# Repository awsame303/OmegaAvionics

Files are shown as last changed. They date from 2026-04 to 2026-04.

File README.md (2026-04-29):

# Omega Avionics — L1 Certification Rocket

Screenshot 2026-04-14 at 5 32 18 PM

A custom-built high-power rocket with a fully designed avionics bay, dual-deployment chute release system, and custom PCB — built to earn an **NAR/Tripoli L1 certification** (H & I class motors) :O

## Overview

This project combines mechanical engineering, embedded systems, and PCB design into a single flight vehicle. The goal is a rocket capable of flying on H and I class motors with onboard data logging, IMU-based orientation tracking, barometric altitude sensing, and an automated parachute deployment system. 

## Purpose

I made it because I wanted to expand my love for rocketry and actually learn a lot about data collection, how to make things that can survive high stress environments, and how to use fillets and other building related things. My ultimate goal for this project is to make a cool rocket that flighs high but also gives me valuable data that I can learn a lot about engineering and aerospace from. I was inspired from my TARC rocketry team, and ultimately wanted to build something with a bit more juice that can fly higher and be more stable. I think that if this goes well, it will be fun to build and assemble. I'm especially excited to paint it, because I heard that it's one of the most challening parts. 

## Hardware

### Avionics PCB



The custom PCB is the heart of the avionics bay, and I Designed it! from scratch in EasyEDA.

Screenshot 2026-04-26 at 9 55 04 AM
> I made another version without RF in case it doesn't work and I made it able to short the pins if I didn't want to use it. In case you were wondering why it wasn't on the PCBA or the BOM

Screenshot 2026-04-26 at 9 55 17 AM

## Firmware

Firmware is written for the ESP32-S3 

## CAD

Full rocket assembly modeled in Onshape
[Link](https://cad.onshape.com/documents/853f342d943e26935c21807b/w/3225035a6dba25a7b5e66f22/e/7ca1891e4b8cbf6983780e85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)

Simulation and stability analysis done in Openrocket



## Certification Goal

This rocket is being built to achieve JKUNIOR Level One High Power Cert through NAR or Tripoli. L1 certification allows ME to purchase and fly H and I class motors independently.

## License

MIT — do whatever u want w it

| Item / Part | Designator | Description / Purpose | Qty | Price | Source |
| :--- | :--- | :--- | :--- | :--- | :--- |
| AMS1117-3.3_C22466222 | U3 | Voltage regulator | 1 | $0.00 | LCSC |
| UBEC | RELE1 | Power module | 1 | $0.00 | LCSC |
| TPS62130RGTRF0 | U1 | Step-down converter | 1 | $0.00 | LCSC |
| ESP32-S3-WROOM-1(N8R2) | U4 | Main microcontroller | 1 | $0.00 | LCSC |
| 2.2uH | U2 | Power inductor | 1 | $0.00 | LCSC |
| 19-217/GHC-YR1S2/3T | LED1 | Status indicator | 1 | $0.00 | LCSC |
| TYPE-C 16PIN 2MD(073) | USB1 | USB interface | 1 | $0.00 | LCSC |
| BMP280 | U6 | Altimeter/Pressure sensor | 1 | $0.00 | LCSC |
| LED-0603_G | LED3 | Status indicator | 1 | $0.00 | LCSC |
| 2700Hz | BUZZER1 | Audible alert | 1 | $0.00 | LCSC |
| 1N4148W | D2 | Signal diode | 1 | $0.00 | LCSC |
| KH-6X6X4.3H-TJ | SW1 | Tactile switch | 1 | $0.00 | LCSC |
| D-MMBT2222A-7-F | U8 | NPN Transistor | 1 | $0.00 | LCSC |
| 470uF | C1 | Electrolytic capacitor | 1 | $0.00 | LCSC |
| 1N5819HW | D1 | Schottky diode | 1 | $0.00 | LCSC |
| Apogee 12in Parachute Protector | | For protecting the parachute from the ejection charge | 1 | $9.66 | Apogee Rocketry |
| emma kites 100% Kevlar Braided String 100Lb | | To attach the rocket to the parachute | 1 | $14.95 | Amazon |
| sprookber Stainless Steel Chain Quick Links | | To attach the parachute cord to the rocket | 1 | $8.99 | Amazon |
| Aero Pack 29/38mm Motor Adapter | | To mount mid power motors (G, F) before testing H class | 1 | $31.85 | Apogee Rocketry |
| 36" Printed Nylon Parachute | | To ensure smooth landing and protect electronics | 1 | $18.69 | Apogee Rocketry |
| Aero Pack 38mm Retainer | | Secures rocket motors during flight | 1 | $30.63 | Apogee Rocketry |
| Bob Smith BSI-205 Slow-Cure Epoxy (30-Min) | | Strong adhesive for structural components | 1 | $13.69 | Amazon |
| J-B Weld 8265S Original Cold-Weld | | Adhesive for miscellaneous parts | 1 | $6.54 | Amazon |
| LOC Forte Kit | | Primary airframe and basic rocket components | 1 | $95.97 | LOC Precision |

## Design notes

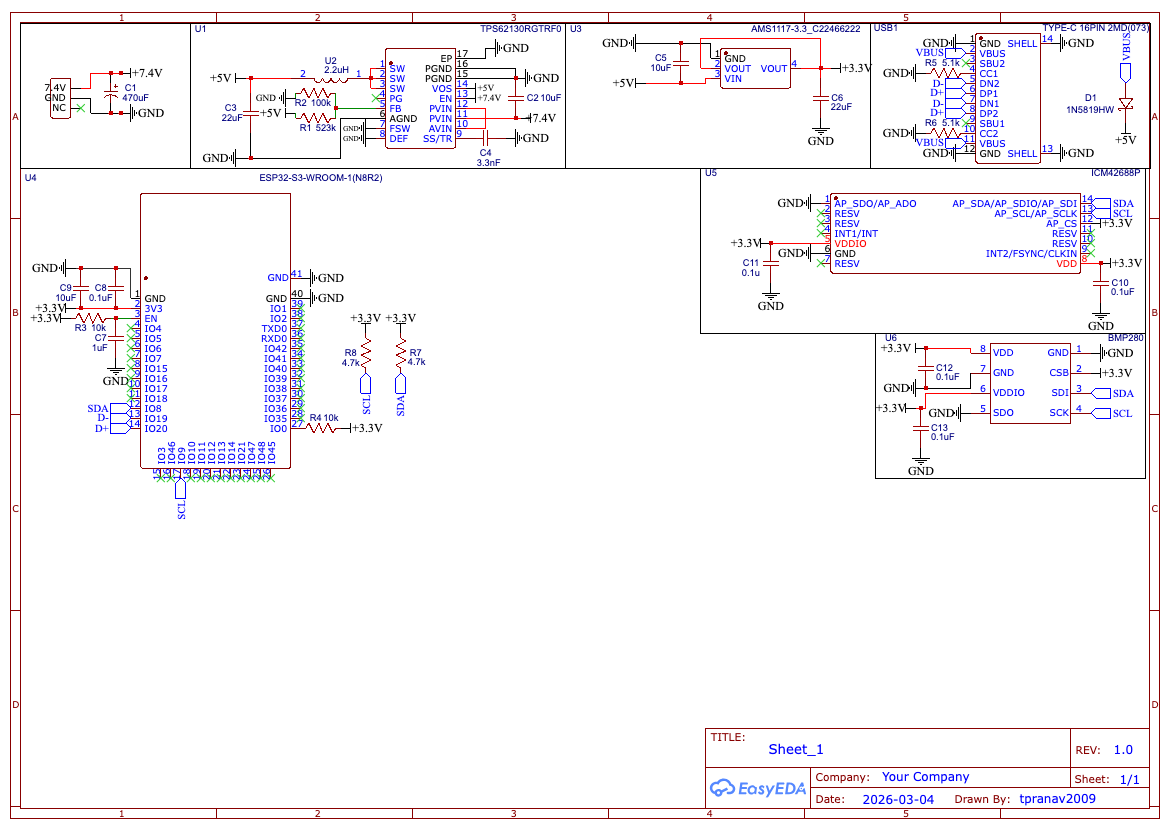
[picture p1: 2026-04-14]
Avionics/PCB/schematic.png

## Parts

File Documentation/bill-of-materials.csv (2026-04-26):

Name | Purpose | Quantity | Total Cost (USD) | Link | Distributor
AMS1117-3.3_C22466222 | U3 | 1 | 0.00 | https://item.szlcsc.com/410724.html | LCSC
UBEC | RELE1 | 1 | 0.00 |  | LCSC
TPS62130RGTRF0 | U1 | 1 | 0.00 | https://item.szlcsc.com/546058.html | LCSC
ESP32-S3-WROOM-1(N8R2) | U4 | 1 | 0.00 | https://www.mouser.cn/datasheet/2/891/Espressif_ESP32_S3_WROOM_1_1U_Preliminary-2530171.pdf | LCSC
2.2uH | U2 | 1 | 0.00 | https://atta.szlcsc.com/upload/public/pdf/source/20220713/554BEAF1208EE235D5D1578E7485E8C7.pdf | LCSC
19-217/GHC-YR1S2/3T | LED1 | 1 | 0.00 | https://item.szlcsc.com/347874.html | LCSC
TYPE-C 16PIN 2MD(073) | USB1 | 1 | 0.00 | https://atta.szlcsc.com/upload/public/pdf/source/20210409/C2765186_34D42616F62DF94D17C4D63D74D9FD03.pdf | LCSC
BMP280 | U6 | 1 | 0.00 | https://atta.szlcsc.com/upload/public/pdf/source/20200702/C83291_F39E84AB7DFC569A4C7554F8659640A1.pdf | LCSC
LED-0603_G | LED3 | 1 | 0.00 |  | LCSC
2700Hz | BUZZER1 | 1 | 0.00 | https://item.szlcsc.com/200842.html | LCSC
1N4148W | D2 | 1 | 0.00 | https://item.szlcsc.com/301422.html | LCSC
KH-6X6X4.3H-TJ | SW1 | 1 | 0.00 | https://item.szlcsc.com/14483.html | LCSC
D-MMBT2222A-7-F | U8 | 1 | 0.00 | https://www.diodes.com/assets/Package-Files/SOT23.pdf | LCSC
470uF | C1 | 1 | 0.00 | https://atta.szlcsc.com/upload/public/pdf/source/20250321/063FCEC07E4987B05CDB75E62EF93118.pdf | LCSC
1N5819HW | D1 | 1 | 0.00 | https://atta.szlcsc.com/upload/public/pdf/source/20210423/C2828417_EF1BF8BE3D48F97E320B09B073C89160.pdf | LCSC
Apogee 12in Parachute Protector | For protecting the parachute from the ejection charge of the parachute so it doesn't get burned | 1 | 9.66 | https://www.apogeerockets.com/Building-Supplies/Parachute-Protection/Cloth/Apogee-12in-Parachute-Protector | Apogee Rocketry
emma kites 100% Kevlar Braided String Utility Cord 100Lb | To attach the rocket to the parachute | 1 | 14.95 | https://www.amazon.com/emma-kites-Braided-Creative-Projects/dp/B01850OSV8/ref=sr_1_1 | Amazon
sprookber Stainless Steel Chain Quick Links | So I can attach the parachute cord to the rocket | 1 | 8.99 | https://www.amazon.com/sprookber-Stainless-Steel-Chain-Quick/dp/B0CM8T6J1R | Amazon
Aero Pack 29/38mm Motor Adapter | So I can mount mid power rocket motorss (G, F) before testing the H class ones | 1 | 31.85 | https://www.apogeerockets.com/Building-Supplies/Motor-Mount-Kits-Adapters/Ready-to-use-Motor-Adapters/Aero-Pack-29-38mm-Motor-Adapter | Apogee Rocketry
36" Printed Nylon Parachute | So the rocket lands smoothly and efficiently and doesn't damage the precious electronics inside. | 1 | 18.69 | https://www.apogeerockets.com/Building-Supplies/Parachutes/Larger-than-24in/36in-Printed-Nylon-Parachute | Apogee Rocketry
Aero Pack 38mm Retainer | For making sure the rocket motors don't fall out mid flight | 1 | 30.63 | https://www.apogeerockets.com/Building_Supplies/Motor_Retainers_Hooks/Screw-on_Retainers_38mm/38mm_AeroPack_Retainer_L | Apogee Rocketry
Bob Smith Industries BSI-205 Slow-Cure™ Epoxy - 4.5 oz. Combined, Clear - 30-Minute Working Time Adhesive for Wood, Fiberglass, Metal, Crafts & Structural Repairs | Gluing all the parts(they need a strong bond so they don't break mid flight) | 1 | 13.69 | https://www.amazon.com/Bob-Smith-Industries-BSI-205-Slow-Cure/dp/B0166FFFS4/ref=sr_1_1 | Amazon
J-B Weld 8265S Original Cold-Weld Steel Reinforced Epoxy - 2 oz | Gluing miscellaneous parts | 1 | 6.54 | https://www.amazon.com/J-B-Weld-8265S-Cold-Weld-Reinforced/dp/B0006O1ICE | Amazon
LOC Forte Kit | Has all the basic parts I need before I add any of the complicated dual deployment, chute release, PCB, or other components. Essentially just wood and cardboard. | 1 | 95.97 | https://locprecision.com/products/forte | LOC Precision

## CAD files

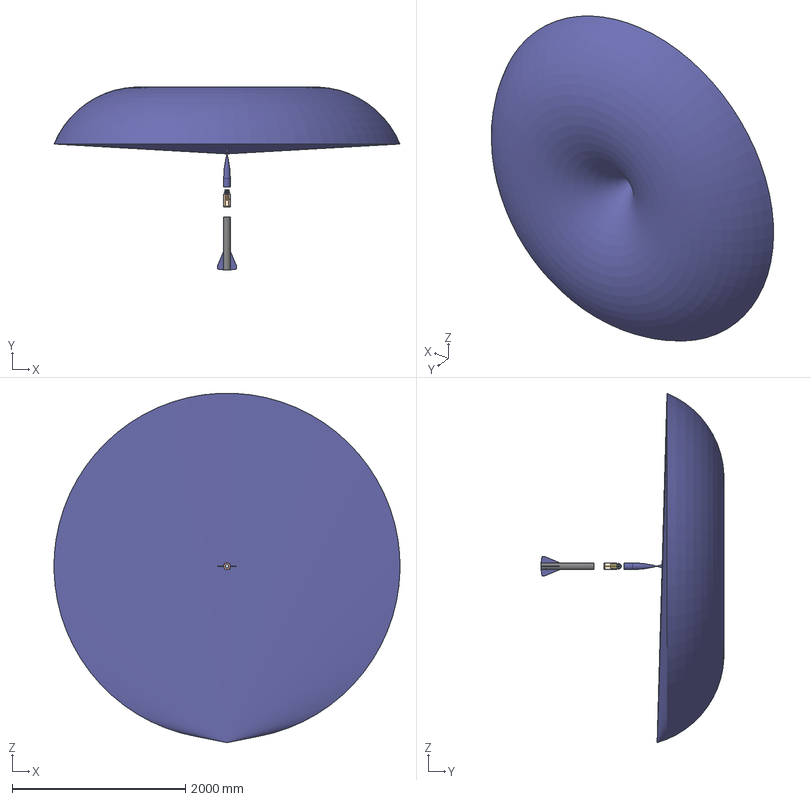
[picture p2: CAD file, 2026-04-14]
Mechanical-Hardware/complete-rocket-assembly.step
3999.3 x 2113.4 x 4037.4 mm
Rail Button x 2
Lower Body Tube
Fin x 4
Centering Ring x 3
Motor Mount
Tube Coupler
Bulkhead
Nose Cone
Rod x 2

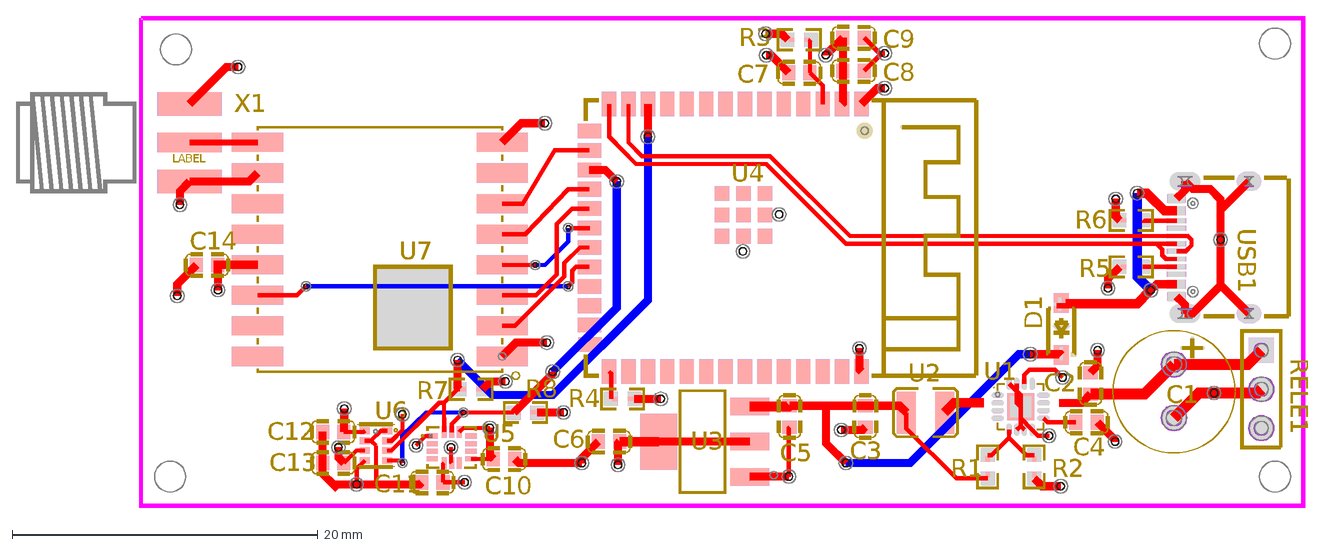
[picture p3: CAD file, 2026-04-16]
Avionics/PCB/pcb-final.dxf
C1
C2
C3
C4
C5
C6
C7
C8
C9
C10
C11
C12
C13
C14
D1
R1
R2
R3
R4
R5
R6
R7
RELE1
U1
U2
U3
U4
U5
U6
U7
USB1
X1
LABEL
R8

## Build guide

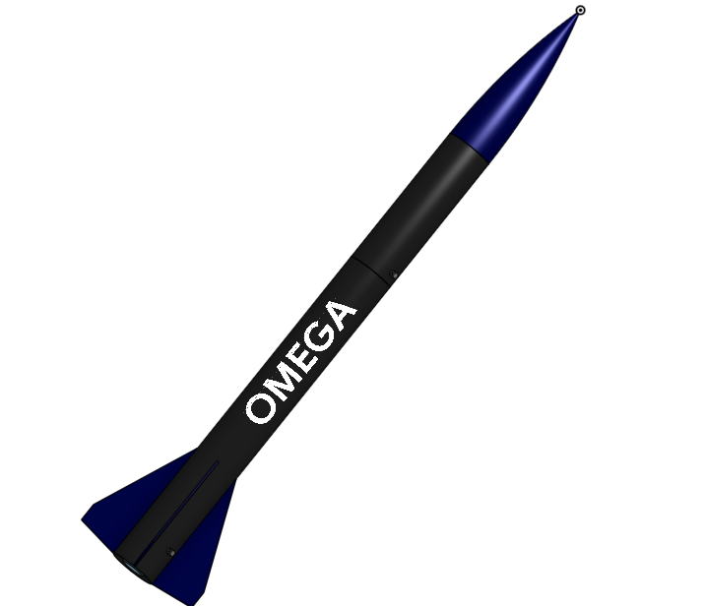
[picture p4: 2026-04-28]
Mechanical-Hardware/complete-rocket-assembly.png

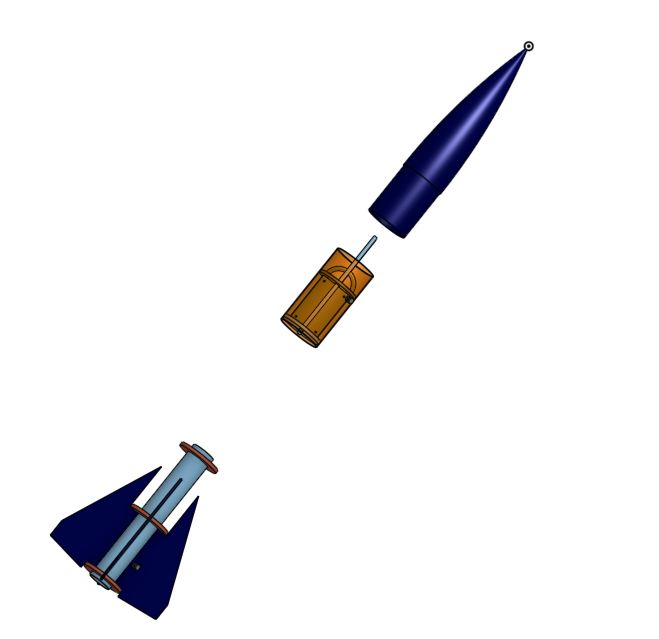
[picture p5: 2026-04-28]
Mechanical-Hardware/complete-rocket-assembly-no-tube.png

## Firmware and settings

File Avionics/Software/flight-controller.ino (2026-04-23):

#include <Wire.h>
#include <SPI.h>
#include <SD.h>
#include <Adafruit_BMP3XX.h>
#include <Servo.h>
#include <MPU6050_light.h>

#define SERVO_PIN 10
#define SD_CS_PIN 4
#define GROUND_PRESSURE_HPA (30.15 * 33.86389)

#define LOOP_DELAY_MS 50
#define DEPLOY_ALT_MIN_FT 300
#define TRIGGER_APOGEE_FT 750
#define PERSIST_COUNT 5

// Physics Constants for 2.27" 560g Rocket
#define ROCKET_MASS_KG 0.560f
#define AREA_M2 0.00261f
#define RHO 1.225f         // Air density kg/m^3

// --- Aerodynamic Drag States ---
// Both set to 0.559 for Flight 1 (No physical deployment)
#define CD_RETRACTED 0.559f 
#define CD_DEPLOYED 0.559f  

#define TWO_KP (2.0f * 0.5f)
#define TWO_KI (2.0f * 0.0f)

Adafruit_BMP3XX bmp;
MPU6050 mpu(Wire);
Servo airbrake;

float groundAlt = 0;
float altitude_m = 0, velocity_mps = 0, acceleration_mps2 = 0;
float prev_alt = 0;
float tilt[3] = { 0 };
float accel[3] = { 0 };

float est_alt = 0, est_vel = 0;
float P = 1, Q = 0.1, R = 3;
unsigned long last_time = 0;

bool deployed = false;
bool retracted = false;
int above750_count = 0;
int below750_count = 0;
float max_alt = 0;
bool apogee_logged = false;

float ax_offset = 0.0f;
float az_offset = 0.0f;

float integralFBx = 0.0f, integralFBy = 0.0f, integralFBz = 0.0f;
float q0 = 1.0f, q1 = 0.0f, q2 = 0.0f, q3 = 0.0f;

float kalmanUpdate(float meas, float &est, float &P) {
  P += Q;
  float K = P / (P + R);
  est += K * (meas - est);
  P *= (1 - K);
  return est;
}

void MahonyAHRSupdateIMU(float gx, float gy, float gz, float ax, float ay, float az, float dt) {
  float recipNorm;
  float halfvx, halfvy, halfvz;
  float halfex, halfey, halfez;

  gx *= 0.0174533f;
  gy *= 0.0174533f;
  gz *= 0.0174533f;

  recipNorm = 1.0f / sqrtf(ax * ax + ay * ay + az * az);
  ax *= recipNorm;
  ay *= recipNorm;
  az *= recipNorm;

  halfvx = q1 * q3 - q0 * q2;
  halfvy = q0 * q1 + q2 * q3;
  halfvz = q0 * q0 - 0.5f + q3 * q3;

  halfex = (ay * halfvz - az * halfvy);
  halfey = (az * halfvx - ax * halfvz);
  halfez = (ax * halfvy - ay * halfvx);

  if (TWO_KI > 0.0f) {
    integralFBx += TWO_KI * halfex * dt;
    integralFBy += TWO_KI * halfey * dt;
    integralFBz += TWO_KI * halfez * dt;
    gx += integralFBx;
    gy += integralFBy;
    gz += integralFBz;
  } else {
    integralFBx = 0.0f;
    integralFBy = 0.0f;
    integralFBz = 0.0f;
  }

  gx += TWO_KP * halfex;
  gy += TWO_KP * halfey;
  gz += TWO_KP * halfez;
  gx *= (0.5f * dt);
  gy *= (0.5f * dt);
  gz *= (0.5f * dt);

  float qa = q0, qb = q1, qc = q2;
  q0 += (-qb * gx - qc * gy - q3 * gz);
  q1 += (qa * gx + qc * gz - q3 * gy);
  q2 += (qa * gy - qb * gz + q3 * gx);
  q3 += (qa * gz + qb * gy - qc * gx);

  recipNorm = 1.0f / sqrtf(q0 * q0 + q1 * q1 + q2 * q2 + q3 * q3);
  q0 *= recipNorm;
  q1 *= recipNorm;
  q2 *= recipNorm;
  q3 *= recipNorm;
}

void clearLogs() {
  if (SD.exists("data.log")) SD.remove("data.log");
  if (SD.exists("apogee.log")) SD.remove("apogee.log");
  File f = SD.open("data.log", FILE_WRITE);
  if (f) {
    f.println(F("time_ms,alt_ft,vel_fps,ax,ay,az,tilt_x_roll,tilt_y_pitch,tilt_z_yaw,pred_apogee_ft"));
    f.close();
  }
}

void setup() {
  Wire.begin();
  delay(10000);
  
  // Force airbrakes completely closed for Flight 1 test
  airbrake.attach(SERVO_PIN);
  airbrake.write(0);
  delay(1000);

  if (!SD.begin(SD_CS_PIN)) {
    while (1);
  }
  clearLogs();

  if (!bmp.begin_I2C(0x77)) {
    while (1);
  }
  bmp.setTemperatureOversampling(BMP3_OVERSAMPLING_2X);
  bmp.setPressureOversampling(BMP3_OVERSAMPLING_4X);
  bmp.setIIRFilterCoeff(BMP3_IIR_FILTER_COEFF_3);

  mpu.begin();
  delay(100);
  mpu.calcOffsets(true, false);

  for (int i = 0; i < 100; i++) {
    mpu.update();
    ax_offset += mpu.getAccX();
    az_offset += mpu.getAccZ();
    delay(10);
  }
  ax_offset /= 100.0f;
  az_offset /= 100.0f;

  for (int i = 0; i < 20; i++) {
    bmp.performReading();
    delay(10);
  }
  bmp.performReading();
  groundAlt = bmp.readAltitude(GROUND_PRESSURE_HPA);
  last_time = millis();
}

void loop() {
  unsigned long t = millis();
  if (t - last_time < LOOP_DELAY_MS) return;
  float dt = (t - last_time) / 1000.0f;
  last_time = t;

  mpu.update();
  bmp.performReading();

  float alt = bmp.readAltitude(GROUND_PRESSURE_HPA) - groundAlt;
  altitude_m = kalmanUpdate(alt, est_alt, P);
  velocity_mps = (altitude_m - prev_alt) / dt;
  acceleration_mps2 = (velocity_mps - est_vel) / dt;
  est_vel = velocity_mps;
  prev_alt = altitude_m;

  float ax_raw = mpu.getAccX() - ax_offset;
  float ay_raw = mpu.getAccY();
  float az_raw = mpu.getAccZ() - az_offset;

  float gx_raw = mpu.getGyroX();
  float gy_raw = mpu.getGyroY();
  float gz_raw = mpu.getGyroZ();

  accel[0] = ax_raw * 9.81f;
  accel[1] = az_raw * 9.81f;
  accel[2] = -ay_raw * 9.81f;

  MahonyAHRSupdateIMU(gx_raw, gz_raw, -gy_raw, ax_raw, az_raw, -ay_raw, dt);

  float roll = atan2f(2.0f * (q0 * q1 + q2 * q3), 1 - 2.0f * (q1 * q1 + q2 * q2)) * 57.29578f;
  float pitch = asinf(2.0f * (q0 * q2 - q3 * q1)) * 57.29578f;
  float yaw = atan2f(2.0f * (q0 * q3 + q1 * q2), 1 - 2.0f * (q2 * q2 + q3 * q3)) * 57.29578f;

  tilt[0] = roll;
  tilt[1] = pitch;
  tilt[2] = yaw;

  // --- APOGEE PREDICTION MATH (NUMERICAL INTEGRATION) ---
  float current_cd = deployed ? CD_DEPLOYED : CD_RETRACTED;
  
  float sim_alt = altitude_m;
  float sim_vel = velocity_mps;
  float sim_dt = 0.1f; // 100ms time step

  // Simulate flight path until apogee
  while (sim_vel > 0) {
    float sim_v_sq = sim_vel * sim_vel;
    float sim_drag_force = 0.5f * RHO * sim_v_sq * current_cd * AREA_M2;
    float sim_drag_decel = sim_drag_force / ROCKET_MASS_KG;
    
    float total_decel = 9.81f + sim_drag_decel;
    
    sim_alt += (sim_vel * sim_dt);
    sim_vel -= (total_decel * sim_dt);
  }

  float predicted_apogee_m = sim_alt;
  float predicted_apogee_ft = predicted_apogee_m * 3.28084f;
  float current_alt_ft = altitude_m * 3.28084f;
  if (altitude_m > max_alt) max_alt = altitude_m;

  // --- DEPLOYMENT LOGIC ---
  if (!deployed && current_alt_ft > DEPLOY_ALT_MIN_FT) {
    if (predicted_apogee_ft > TRIGGER_APOGEE_FT) {
      above750_count++;
    } else {
      if (above750_count > 0) above750_count--;
    }

    if (above750_count >= PERSIST_COUNT) {
      // Logic triggers, but flaps are disconnected/zeroed for Flight 1 testing
      // airbrake.write(120); 
      deployed = true;
    }
  }

  // --- RETRACTION LOGIC ---
  if (deployed && !retracted) {
    if (predicted_apogee_ft < (TRIGGER_APOGEE_FT - 5)) {  // 5ft Buffer
      below750_count++;
    } else {
      if (below750_count > 0) below750_count--;
    }

    if (below750_count >= 5) {  // Matching the 5 solid readings from the Python script
      // airbrake.write(0);
      retracted = true;
    }
  }

  File f = SD.open("data.log", FILE_WRITE);
  if (f) {
    f.print(t);
    f.print(',');
    f.print(current_alt_ft, 1);
    f.print(',');
    f.print(velocity_mps * 3.28084f, 1);
    f.print(',');
    f.print(accel[0], 2);
    f.print(',');
    f.print(accel[1], 2);
    f.print(',');
    f.print(accel[2], 2);
    f.print(',');
    f.print(tilt[0], 1);
    f.print(',');
    f.print(tilt[1], 1);
    f.print(',');
    f.print(tilt[2], 1);
    f.print(',');
    f.println(predicted_apogee_ft, 1);
    f.close();
  }

  if (!apogee_logged && est_vel < 0 && acceleration_mps2 < -0.2f && max_alt >= 100) {
    File af = SD.open("apogee.log", FILE_WRITE);
    if (af) {
      af.print(F("Apogee(ft): "));
      af.println(max_alt * 3.28084f, 1);
      af.close();
    }
    apogee_logged = true;
  }
}

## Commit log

2026-04-14 Rocket Assembly
    [Assembly.step]
2026-04-14 Current Design Schematic for PCB
2026-04-14 README
    Added detailed project overview, hardware specifications, firmware information, CAD challenges, build log, and certification goal for the Omega Avionics rocket.
2026-04-14 Rocketry PCB
    VERY EARLY STAGE NOT MUCH THINGS ADDED YET
    [pcbRocketry.pcbdoc]
2026-04-16 Rocket PCB FINISHED
    Rocket PCB FINISHED!! Super happy
    [RocketPCB.dxf]
2026-04-26 Enhance README with PCB design details and images
    Added additional images and details about the custom PCB design and its alternatives.
2026-04-26 Add BOM Csv
    [L1 Certification Rocket-bom.csv]
2026-04-28 fixed project structure
    [bill-of-materials.csv, complete-rocket-assembly.step, pcb-final.dxf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]
2026-04-29 Update README with CAD link and simulation info
    Added link to CAD document and included simulation details.
